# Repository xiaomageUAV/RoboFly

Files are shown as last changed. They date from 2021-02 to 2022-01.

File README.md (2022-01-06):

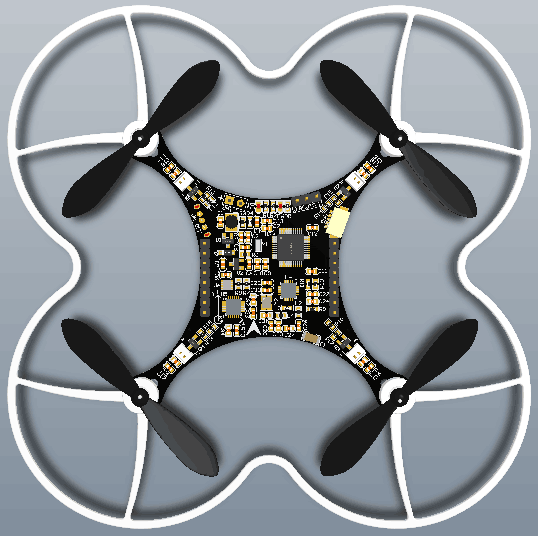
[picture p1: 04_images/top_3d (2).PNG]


# 简介

RoboFly是小马哥在2018年8月推出的一款完全开源的小四轴。

这款小四轴开发的初衷是为了让大家更低成本的通过一个完整的小项目来学习电路板设计、STM32编程开发、四轴飞行器的基本原理等知识。

# RoboFly的硬件架构

主控：STM32F103C8T6(没错，就是在2020年底因缺货疯狂涨价的的芯片之一)

姿态传感器：MPU6050

气压计：SPL06/FBM32/BMP280

无线通讯：2.4G

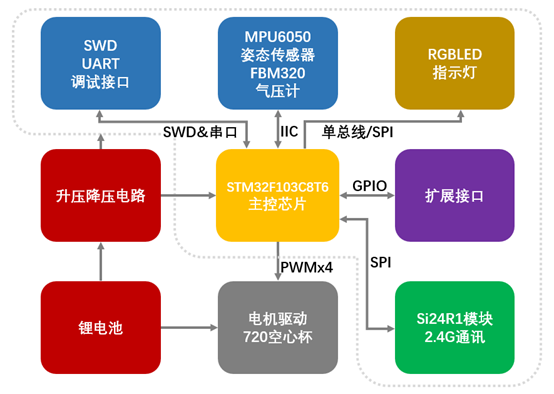
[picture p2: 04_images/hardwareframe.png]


# 开发说明

硬件设计软件为Altium Designer

程序文件使用Keil 打开即可，需要自行安装相关库。

因尺寸限制，STM32F013C8T6下载程序接口为SH1.0 5P端子口，配合e-Link32烧录器进行下载即可。

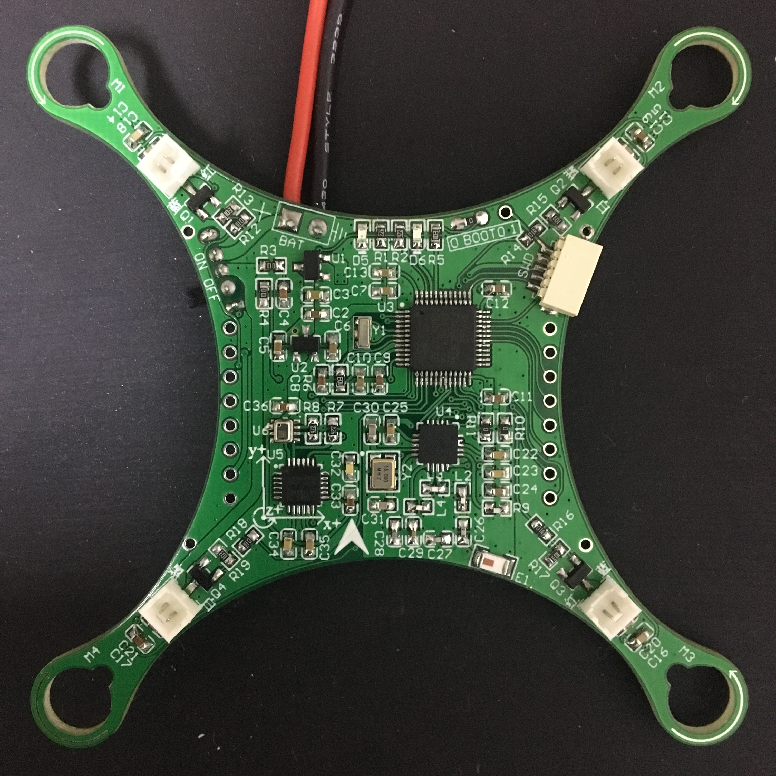
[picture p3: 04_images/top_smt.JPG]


# 打样焊接装配说明

PCB为两层板，通用工艺，基本上所有板厂都可以加工打样，成本低廉。板子用到的阻容器件最小为0603，而且在布局的时候已经考虑手工焊接的因素，布局较为松散，方便焊接。

板子上除了气压计使用烙铁焊接有一点难度之外，其他所有器件基本可以使用烙铁焊接完成。推荐使用刀头烙铁进行焊接。

焊接装配参考下图进行即可

###### 注意事项：气压计1脚标识在肚子上，而不是铁壳上的气孔。如果错误的把气孔当作1脚标识，可能会焊接反了导致板子上3.3V对地短路。

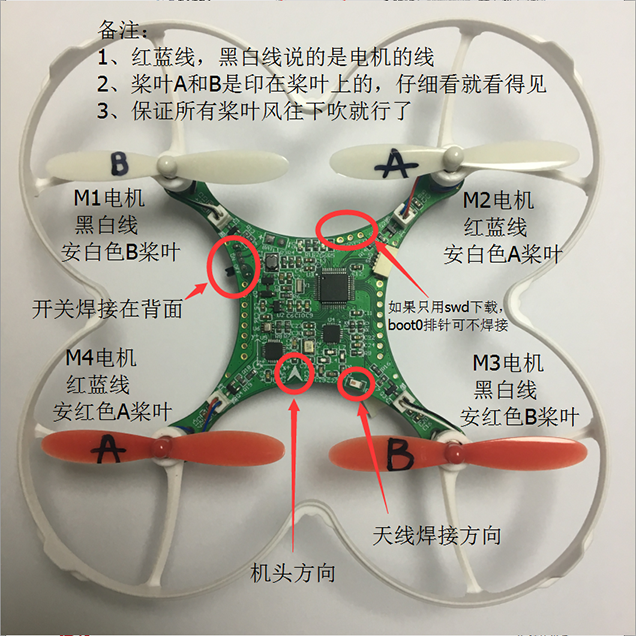
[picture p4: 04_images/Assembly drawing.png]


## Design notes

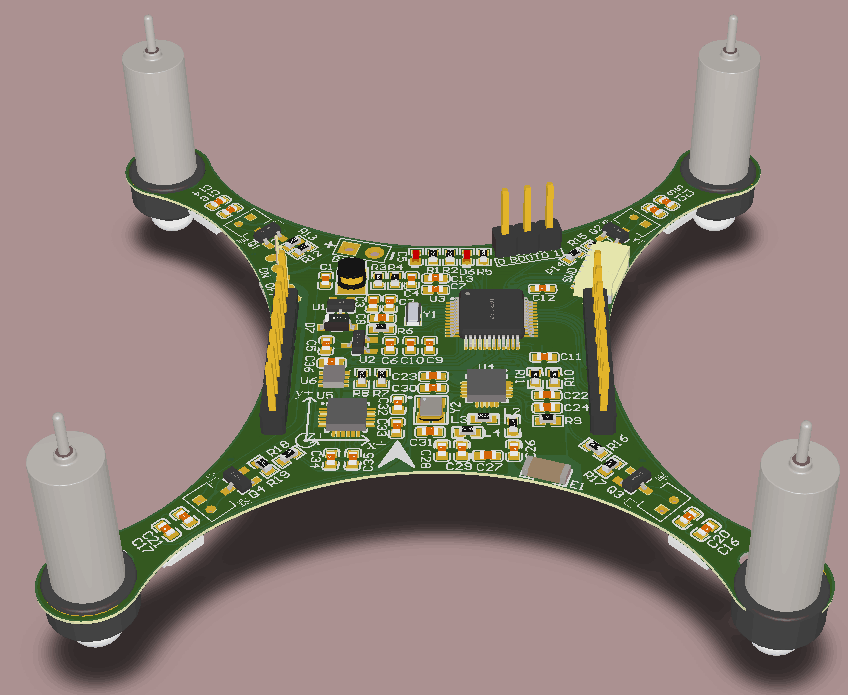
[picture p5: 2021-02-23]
04_images/3d.PNG

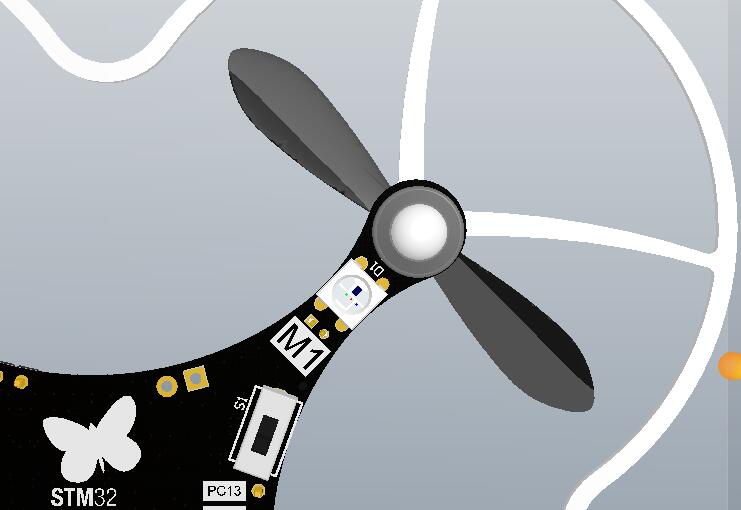
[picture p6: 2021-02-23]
04_images/motor.JPG

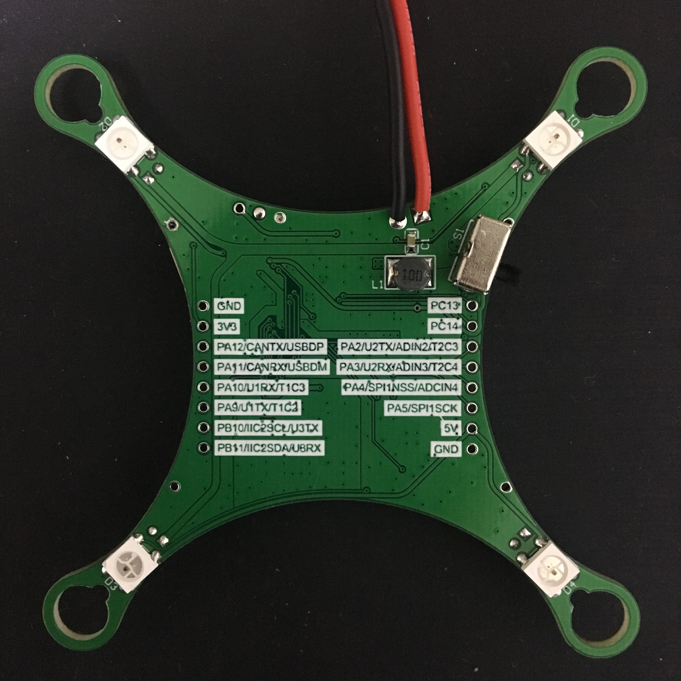
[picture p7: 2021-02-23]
04_images/bottom.JPG

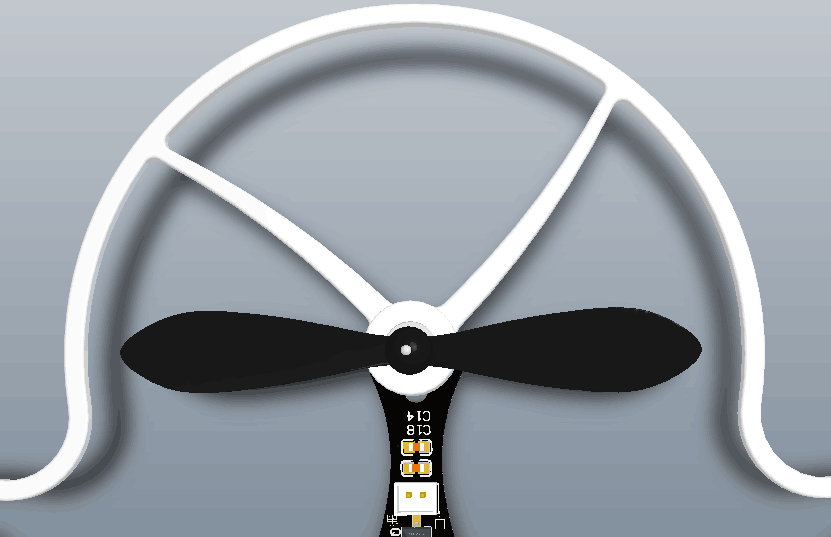
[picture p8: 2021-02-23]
04_images/paddle.PNG

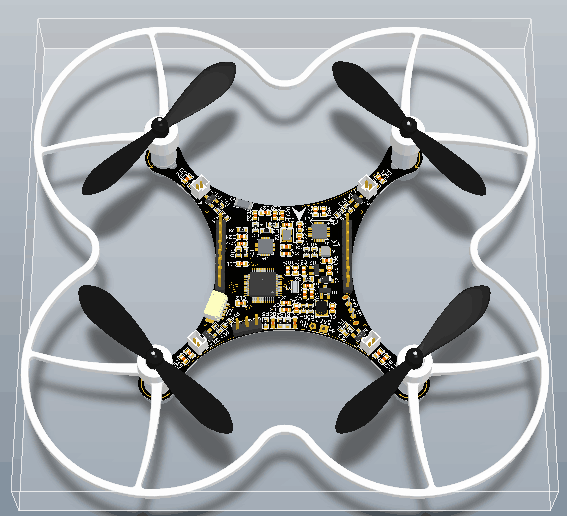
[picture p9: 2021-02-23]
04_images/3d (2).PNG

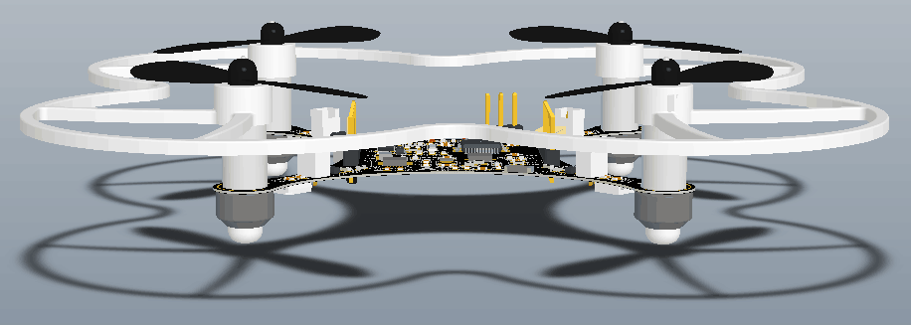
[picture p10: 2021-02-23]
04_images/3d_2.PNG

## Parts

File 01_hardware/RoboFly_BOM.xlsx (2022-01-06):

RoboFly开源四轴BOM表-小马哥(交流群：829018006)
包序号 | Name | Comment | Designator | Footprint | Value | QTY | 配货数量
4 | 电池600mAh |  |  |  |  | 1 | 1
5 | 720空心杯 | Motor_720 | M1, M2, M3, M4 | MOTOR |  | 4 | 4
 | 电机插座 |  |  |  |  | 4 | 4
6 | 电机保护垫 |  |  |  |  | 4 | 4
7 | 55mm桨叶 |  |  |  |  | 4 | 4
8 | 桨叶保护罩 |  |  |  |  | 1 | 1
9 | 主控芯片 | STM32F103C8 | U3 | LQFP-48 |  | 1 | 1
10 | 陀螺仪 | MPU6050 | U5 | QFN-24 |  | 1 | 1
11 | 气压计 | FBM320 | U6 | LGA-8 |  | 1 | 1
12 | 2.4G芯片 | Si24R1 | U4 | QFN20 |  | 1 | 1
13 | 贴片电阻 | R_0603 | R1, R2, R7, R8 | R_0603 | 4.7K | 4 | 7
 | 贴片电阻 | R_0603 | R3, R4 | R_0603 | 100K,1% | 2 | 3
 | 贴片电阻 | R_0603 | R5, R6, R13, R15, R17, R19 | R_0603 | 10K | 6 | 9
 | 贴片电阻 | R_0603 | R9 | R_0603 | 22K | 1 | 2
 | 贴片电阻 | R_0603 | R10, R11 | R_0603 | 0R | 2 | 4
 | 贴片电阻 | R_0603 | R12, R14, R16, R18 | R_0603 | 100R | 4 | 6
14 | 贴片电容 | C_0603 | C27 | C_0603 | 1pF | 1 | 4
 | 贴片电容 | C_0603 | C26 | C_0603 | 1.5pF | 1 | 3
 | 贴片电容 | C_0603 | C29 | C_0603 | 4.7pF | 1 | 2
 | 贴片电容 | C_0603 | C30, C31 | C_0603 | 10pF | 2 | 5
15 | 贴片电容 | C_0603 | C24 | C_0603 | 1nF | 1 | 2
 | 贴片电容 | C_0603 | C28, C32 | C_0603 | 2.2nF | 2 | 4
 | 贴片电容 | C_0603 | C34 | C_0603 | 10nF | 1 | 3
16 | 贴片电容 | C_0603 | C3, C4, C7, C8, C10, C11, C12, C13,C14, C15, C16, C17, C23, C33, C35, C36 | C_0603 | 0.1uF | 16 | 20
 | 贴片电容 | C_0603 | C5, C6, C9 | C_0603 | 1uF | 3 | 5
 | 贴片电容 | C_0603 | C18, C19, C20, C21, C22 | C_0603 | 4.7uF | 5 | 8
 | 贴片电容 | C_0603 | C1 | C_0603 | 10uF | 1 | 2
 | 贴片电容 | C_0603 | C2 | C_0603 | 22uF | 1 | 3
17 | 2.4G陶瓷天线 | ANT | E1 | ANT |  | 1 | 1
 | 绕线电感 | Inductor | L1 | L_1210 | 4.7uH | 1 | 1
 | 贴片电感 | Inductor | L4 | L_0603 | 2.7nH | 1 | 4
 | 贴片电感 | Inductor | L2 | L_0603 | 3.9nH | 1 | 3
 | 贴片电感 | Inductor | L3 | L_0603 | 8.2nH | 1 | 2
18 | 卧式开关 | SW-SPDT | S1 |  |  | 1 | 1
 | 跳线帽 | BOOT | BOOT0 |  |  | 1 | 1
 | E-Link下载口 | SWD | SWD |  |  | 1 | 1
 | 电池母线 | BAT | BAT |  |  | 1 | 1
 | 排针 | Header 1 | P1, P2, P3, P4, P5, P6, P7, P8, P9, P10, P11, P12, P13, P14, P15, P16 |  |  | 16 | 1
19 | MOS管 | SI2302 | Q1, Q2, Q3, Q4 | SOT-23-3 |  | 4 | 6
 | 二极管 | 1N4148 | D7 | SOD-123 |  | 1 | 1
 | 红色LED | 红色 | D5 | LED-0603 |  | 1 | 3
 | 绿色LED | 绿色 | D6 | LED-0603 |  | 1 | 2
 | RGBLED | P923D | D1, D2, D3, D4 | 5050 |  | 4 | 6
20 | 升压芯片 | XT1861B502MR-G | U1 | SOT-23-3 | 丝印AXMD | 1 | 1
 | 线性稳压芯片 | XC6206 | U2 | SOT-23-3 | 丝印662K | 1 | 1
21 | 8M晶振 | XTAL | Y1 | SMD | 8MHz | 1 | 1
 | 16M晶振 | XTAL | Y2 | 3225_4P | 16MHz | 1 | 1
22 | PCB空板 |  |  |  |  | 1 | 1
23 | elink32 |  |  |  |  | 1 | 1
24 | 一拖四充电器 |  |  |  |  | 1 | 1
备注： 1、包16中增加了22uf电容,建议焊接时给C1处贴22uF电容； 2、包15中去掉了33nf电容； 3、boot开关换为跳线帽，去掉了立式开关； 4、包18中增加了一个电池母线； 5、包19中增加一个红色二极管； 6、包19中增加了二极管1N4148； 7、包20中HT7750SA换为XT1861B502MR-G，丝印为AXMD

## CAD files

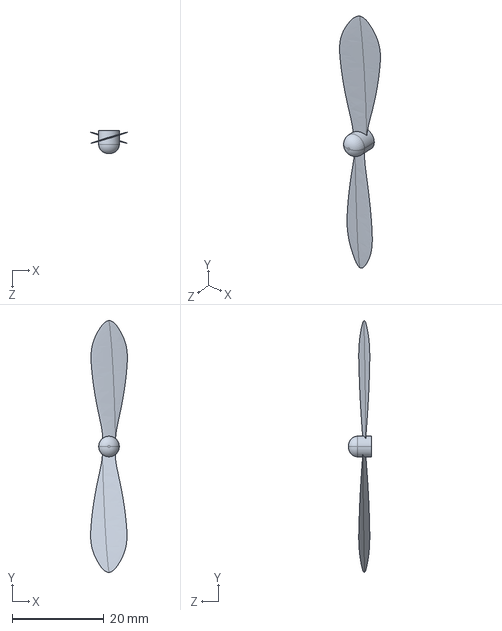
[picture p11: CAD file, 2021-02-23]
03_structure/B桨叶.STEP
8.02 x 55.0 x 5.00 mm

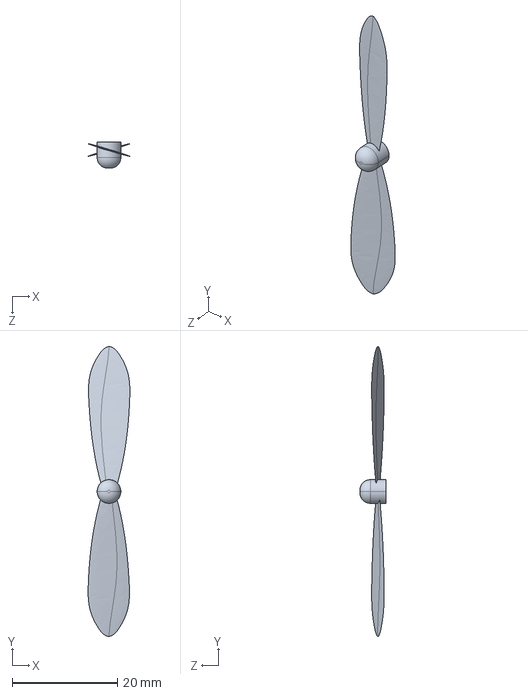
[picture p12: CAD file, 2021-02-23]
03_structure/A桨叶.STEP
7.92 x 55.0 x 5.00 mm

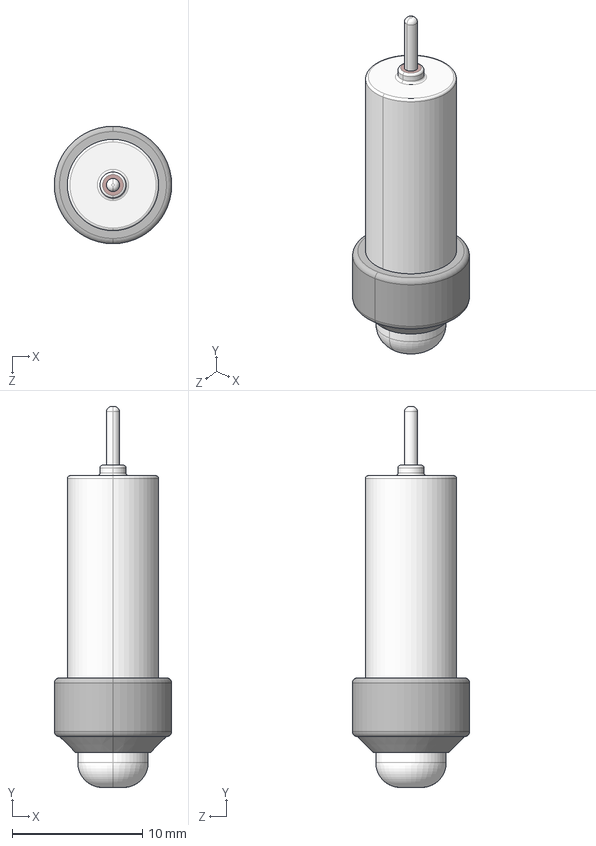
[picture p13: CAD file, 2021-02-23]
03_structure/720空心杯电机.STEP
9.00 x 29.2 x 9.00 mm

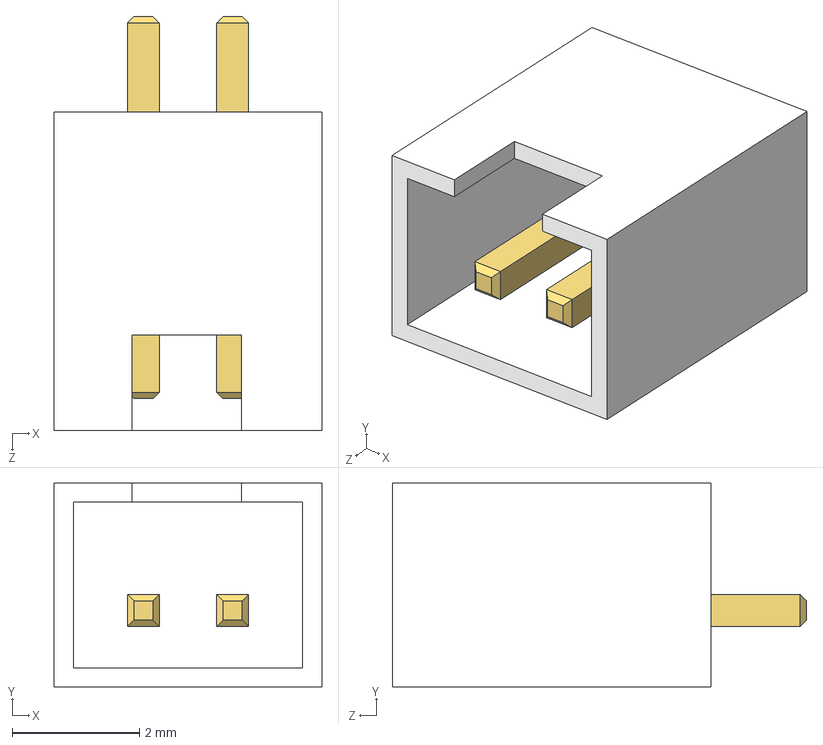
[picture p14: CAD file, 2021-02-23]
03_structure/电机插座.STEP
4.20 x 3.20 x 6.50 mm

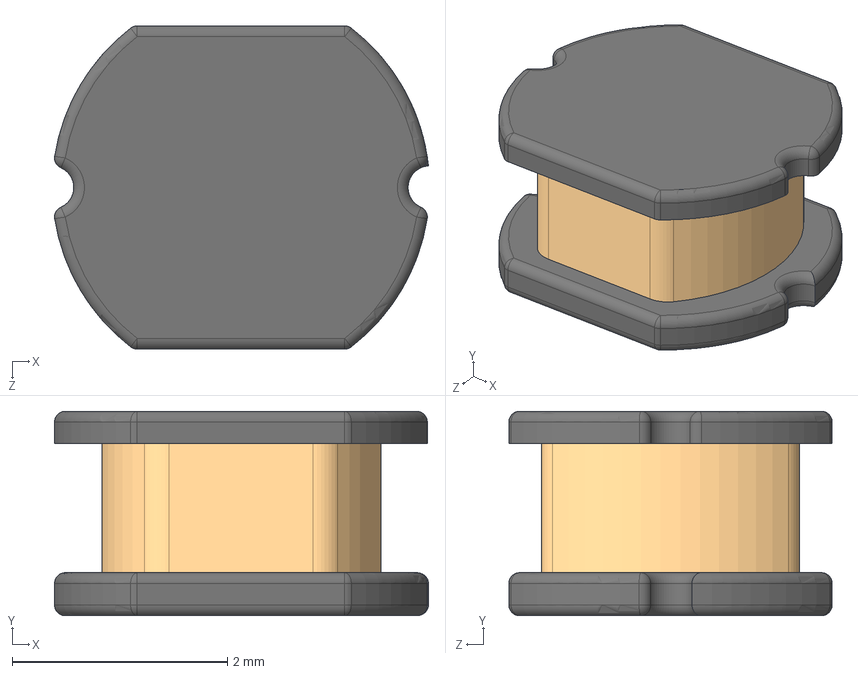
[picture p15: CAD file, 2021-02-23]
03_structure/电感.STEP
3.48 x 1.90 x 3.00 mm

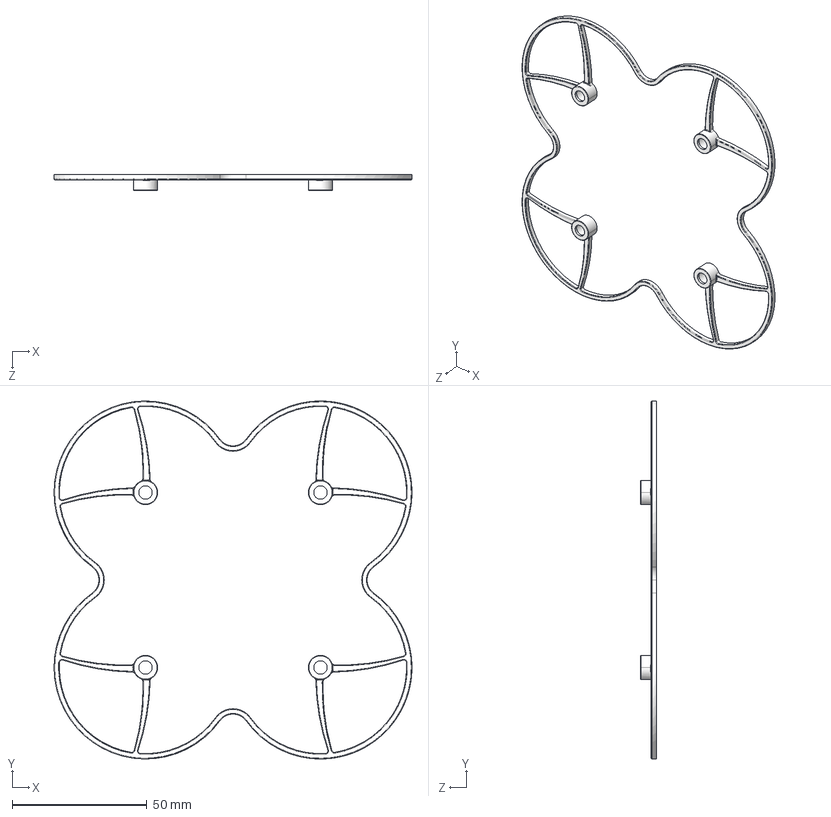
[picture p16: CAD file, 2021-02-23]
03_structure/桨叶保护罩.STEP
133.0 x 133.0 x 6.00 mm

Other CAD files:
03_structure/720空心杯电机.SLDPRT
03_structure/A桨叶.SLDPRT
03_structure/B桨叶.SLDPRT
03_structure/桨叶保护罩.SLDPRT
03_structure/电感.SLDPRT
03_structure/电机插座.SLDPRT

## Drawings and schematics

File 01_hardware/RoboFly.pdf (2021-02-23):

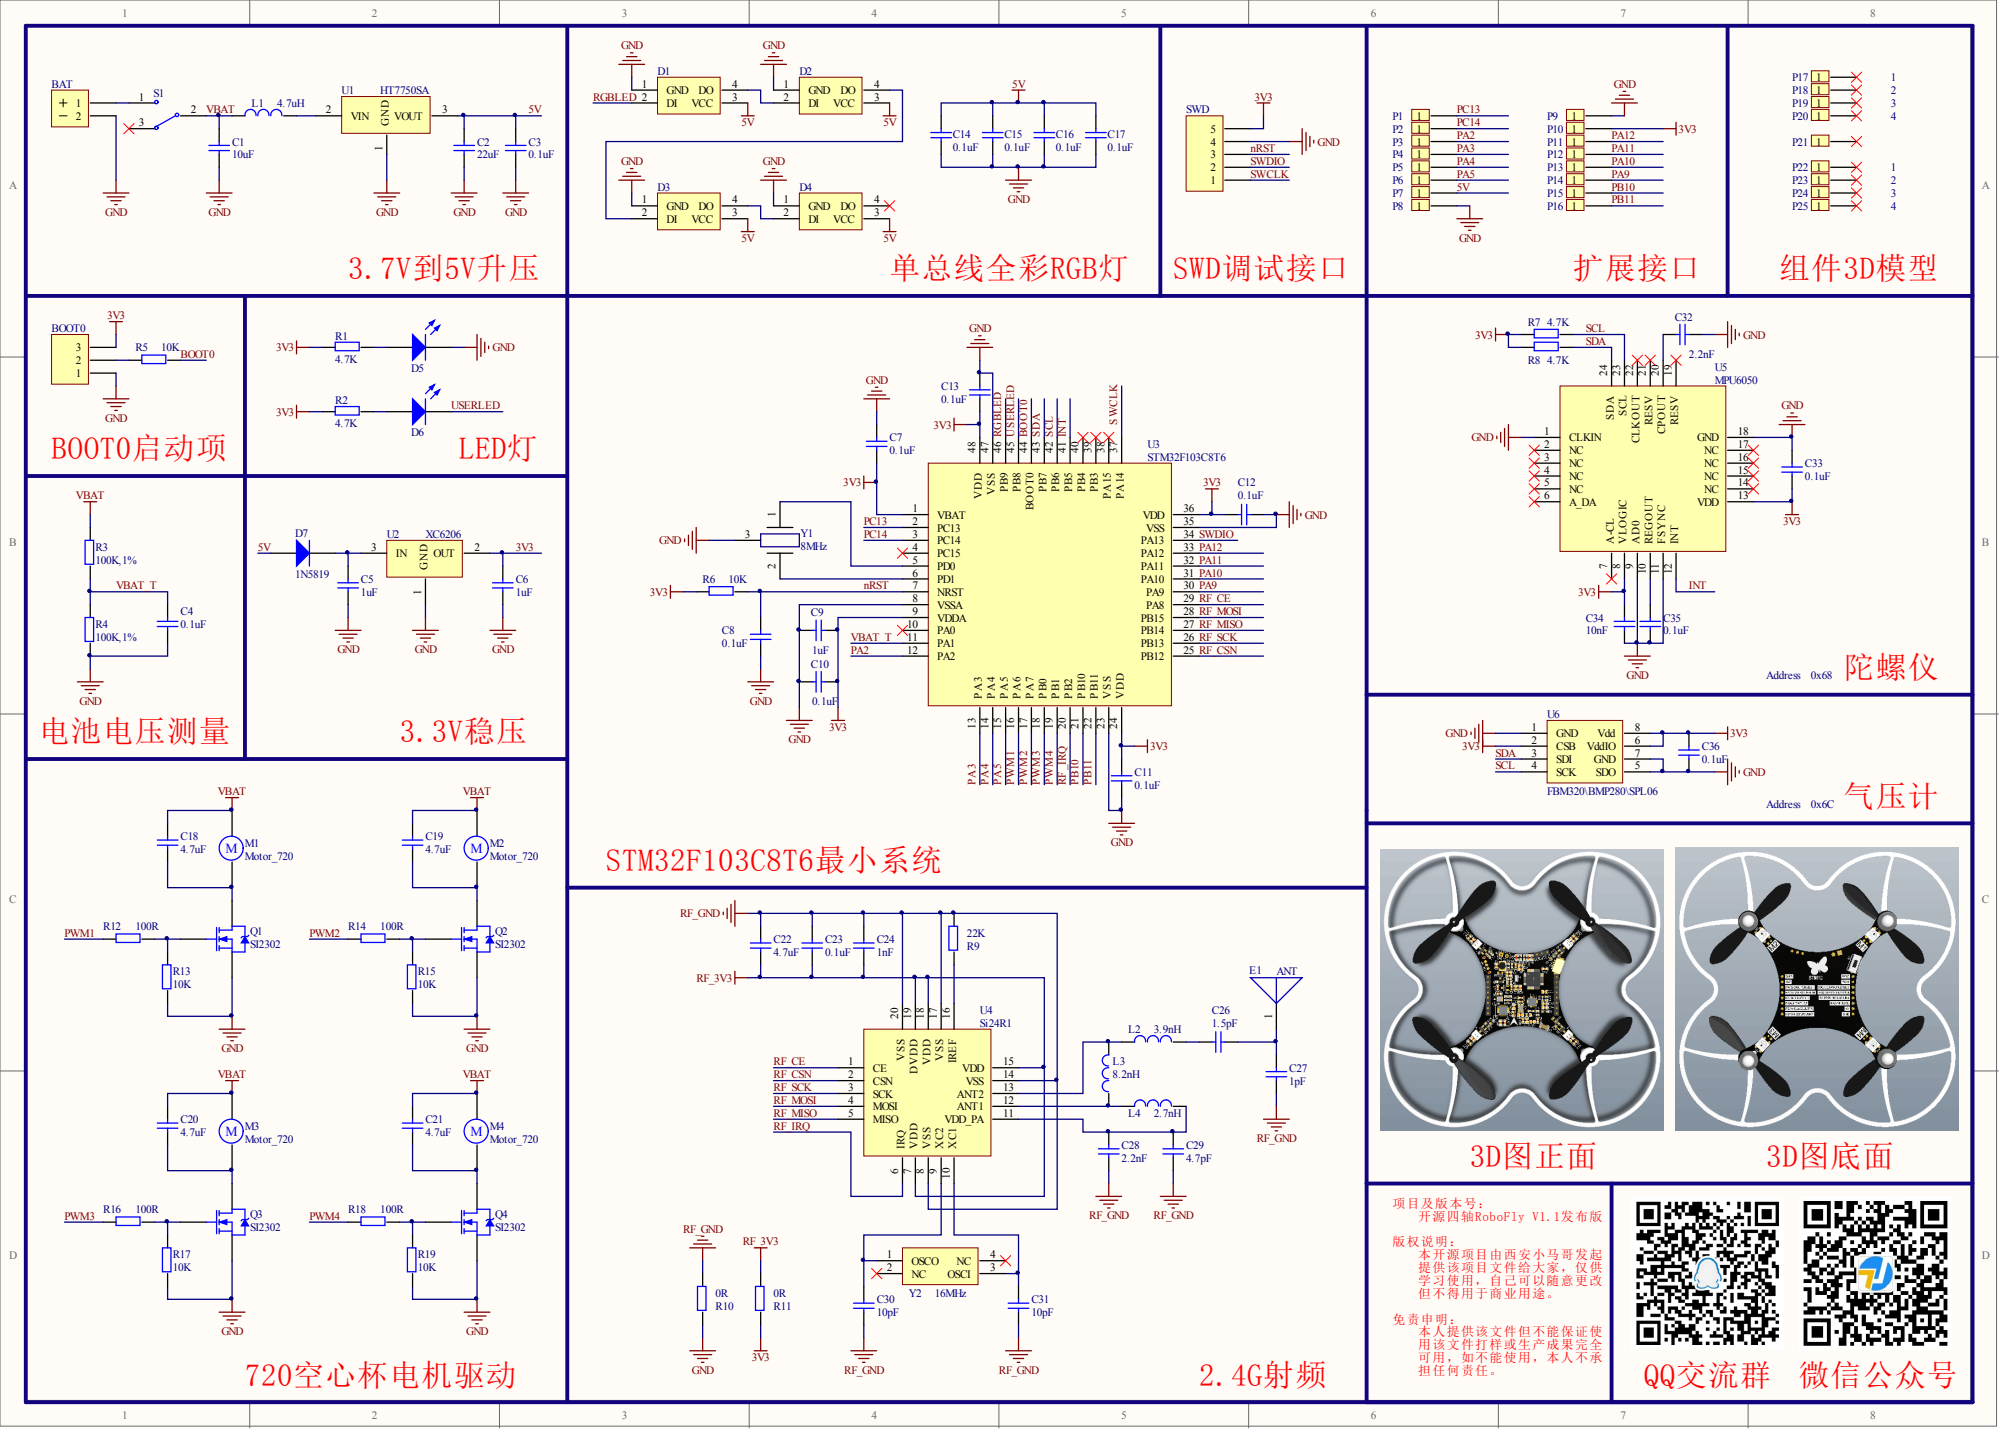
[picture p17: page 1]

VSSA 8 | RF_CE

C9 | | VDDA 9 | RF_MOSI
1uF C10 | | VBAT_T PA2 | PA0 10 | RF_MISO

15 REF 16 VSS 17 VDD 18 DVDD 19 VSS 20

OSCO 1 | OSCI

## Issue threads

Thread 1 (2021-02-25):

关于无法使用串口下载程序的BUG

xiaomageUAV, 2021-02-25:
STM32使用串口下载程序需要把BOOT0和BOOT1做如下配置：

- BOOT0：高电平
- BOOT1：低电平

但是在RoboFly中，BOOT1即PB2作为SI24R1的IRQ信号输入引脚使用。在SI24R1中这个引脚内置了上拉电阻，所以单片机上电的时候，PB2会检测到高电平，无法进入串口下载。因为SI24R1芯片内部有上拉电阻，所以通过外置下拉电阻的方式也不能实现启动时BOOT1配置为低电平。

可行的办法就是在上电之前把BOOT1直接接地（不要通过电阻下拉），然后把BOOT0接高电平，就可以使用串口下载了。

后续在进行PCB设计的时候，可以把PB2更换为其他功能，避开SI24R1的IRQ信号。

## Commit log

2021-02-23 first push
    [720空心杯电机.SLDPRT, 720空心杯电机.STEP, A桨叶.SLDPRT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]
2022-01-06 5V升压芯片由HT7750SA更换为XT1861B502MR-G,并更新BOM表
    [RoboFly_BOM.xlsx]
